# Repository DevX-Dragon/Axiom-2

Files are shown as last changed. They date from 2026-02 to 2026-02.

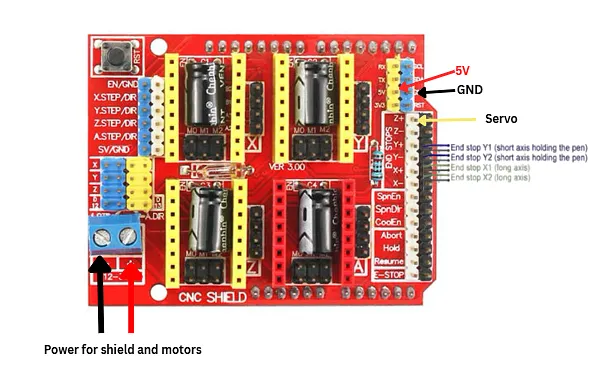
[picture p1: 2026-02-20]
images/CNC Wiring Diagram.png

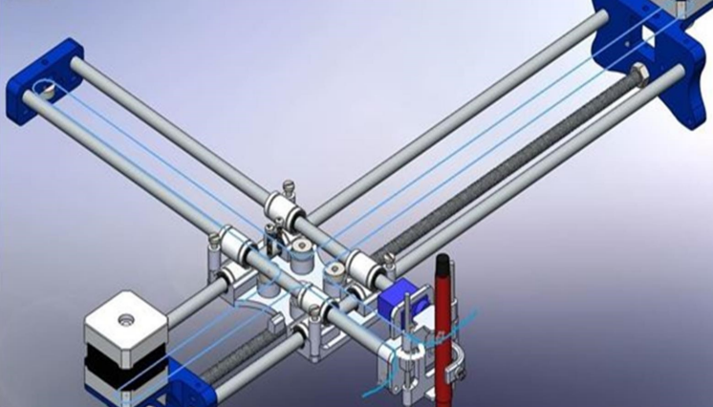
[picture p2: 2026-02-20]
images/BELT DIAGRAM.png

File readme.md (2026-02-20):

# Axiom-2 🤖🖊️
YO. Welcome to Axiom-2. It’s a CNC drawing machine that basically does my homework (not really, don't tell my teacher). I built this because I wanted a robot that draws better than me.

## What is this?
It’s a "Drawing Bot" that uses an Arduino Uno and a CNC Shield to move a pen around. It runs on GRBL (which is basically the brain) with some tiny tweaks I made so it doesn't freak out.

## Images
### Full Render
Full Render
(still in prodcution so not fully rendered)

### Belt Diagrams
Belt Diagram EXCIL DRAW 2
BELT DIAGRAM

### CNC Overview
CNC Wiring Diagram

## Cool Stuff Inside
**The Brain:** Arduino Uno + CNC Shield (v3)

**Firmware:** GRBL (hacked a bit)

**The Parts:** I put the BOM (Bill of Materials) in the .xlsx file above. It has all the nuts, bolts, and rods you need to buy.

**Pictures:** Check the /images folder to see what it actually looks like.

## How to use it (I think)
**Flash it:** Get the GRBL firmware onto the Arduino.

**Wire it:** Plug the stepper motors into the shield. Don't blow it up.

**Software:** Use something like Universal Gcode Sender (UGS) to send your drawings to the bot.

**Draw:** Put a pen in the holder and watch it go zoom.

## Hardware
I put the CAD files/designs in the /hardware folder. If you have a 3D printer, you can probably make this yourself.

## 🛠️ Axiom-2 Official BOM (with links!!)

| Product Name | Qty | Price (ea) | Total | Notes |
| :--- | :---: | :--- | :--- | :--- |
| [**Nema 17 Stepper Motor**](https://www.duino.lk/product/nema-17-stepper-motor-bipolar-1-8deg-1-5a-42ncm-42x42x40mm/) | 2 | $8.07 | $16.14 | Bipolar version |
| [**Linear Rod M8 (1m)**](https://www.duino.lk/product/1000mm-8mm-smooth-shaft/) | 2 | $5.81 | $11.62 | Need 2x 450mm and 2x 350mm |
| **Linear Rod 3mm** | 2 | - | $0.00 | Salvaging from a CDROM |
| **Threaded Rod M8 x 480mm** | 1 | - | $0.00 | Still haven't found a link for this |
| [**LM8UU Bearings**](https://www.duino.lk/product/lm8luu-lm20luu-ball-bearings/) | 8 | $1.45 | $11.60 | Standard sliders |
| [**SG90 Servo Motor**](https://www.duino.lk/product/servo-motor-sg90-9g-micro-servo-motor/) | 1 | $1.81 | $1.81 | Pen lift go brrrr |
| **Spring** | 1 | - | $0.00 | From a ballpoint pen lol |
| [**GT2 Pulley (16T)**](https://www.duino.lk/product/gt2-16t-16-teeth-5mm-bore/) | 2 | $0.97 | $1.94 | 5mm bore |
| [**Bearing 624zz**](https://www.duino.lk/product/624zz-ball-bearing/) | 5 | $0.48 | $2.40 | Tiny bearings |
| [**GT2 Belt (1m)**](https://www.duino.lk/product/gt2-6mm-width-2gt-pu-transmission-timing-belt/) | 2 | $1.61 | $3.22 | Buying 2m total |
| [**CNC Shield + Uno + Drivers**](https://www.duino.lk/product/cnc-shield-v3-0-uno-r3-4pcs-a4988-drivers/) | 1 | $20.97 | $20.97 | Cheaper as a kit |
| [**Jumper Connectors**](https://www.duino.lk/product/2-pin-jumper-connector-stud-2-54mm-standard/) | 1 | $0.32 | $0.32 | |
| [**12V 2A Power Supply**](https://www.duino.lk/product/power-supply-adapter-3-pin-ac-dc-12v-2a/) | 1 | $2.42 | $2.42 | |
| **3D Printing (Legion)** | 1 | $30.00 | $30.00 | |
| **Exchange Tax** | - | - | $5.00 | |
| **Shipping** | - | - | $5.00 | |
| **TOTAL** | | | **$112.44** | |
> (THIS IS USING A LOCAL ONLY ELECTRONICS STORE. IF YOU'RE GOING TO HAVE TO SOURCE IT YOURSELF. USE AMAZON , ALIEXPRESS , TEMU)
> THERE ARE STILL NUTS , WASHERS , ETC YOU NEED BUY SEPERATELY

Made by DevX-Dragon 🐉
(If it breaks, its not my fault lol)

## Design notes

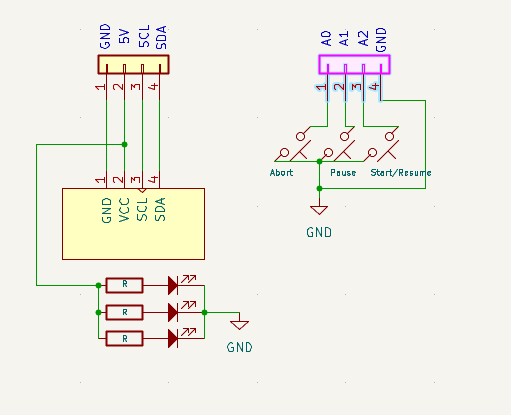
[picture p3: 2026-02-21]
images/Controller Board Schematics.png

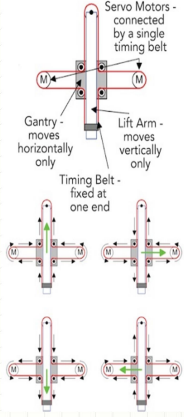
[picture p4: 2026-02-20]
images/Belt Diagram EXCIL DRAW 2.png

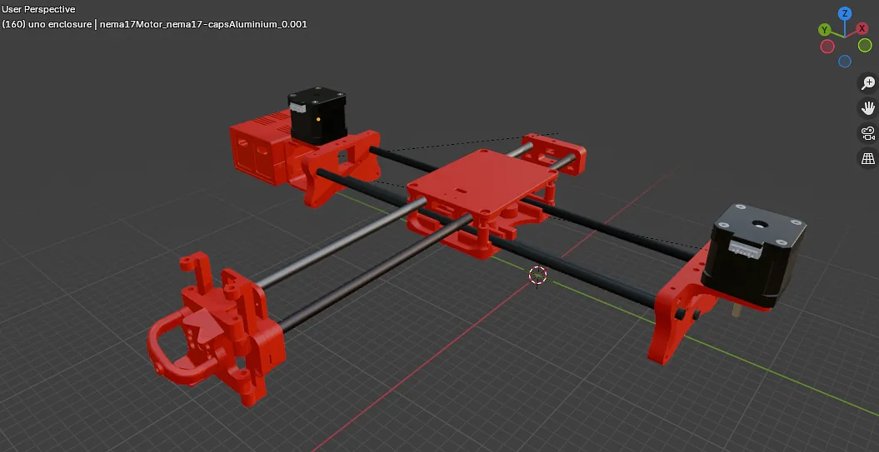
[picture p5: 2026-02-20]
images/Full Render.png

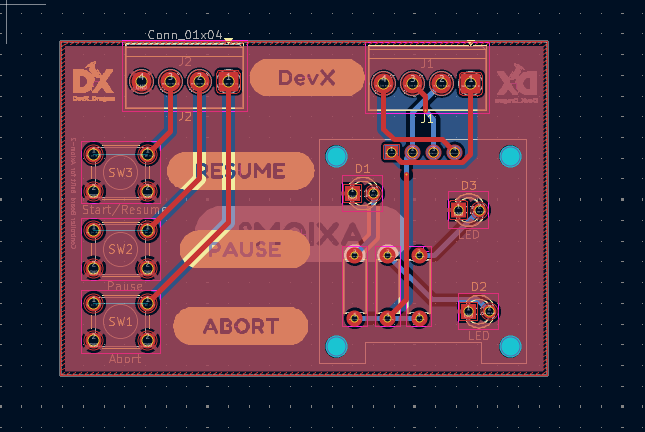
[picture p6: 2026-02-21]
images/Controller Board PCB.png

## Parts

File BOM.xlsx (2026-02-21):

Product Name | Quanity | Price Per Unit | Total Price | Link | Additional Notes
Nema 17 Stepper Motor Bipolar 1.8deg 1.5A 42Ncm 42x42x40mm 4 Wires with 1m | 2 | $8.07 | $16.14 | https://www.duino.lk/product/nema-17-stepper-motor-bipolar-1-8deg-1-5a-42ncm-42x42x40mm/ | bipolar version
Linear Rod M8 x 450mm + 350mm | 2 | $5.81 | $11.62 | https://www.duino.lk/product/1000mm-8mm-smooth-shaft/ | I need x2 450mm and x2 350mm for x and y axis. Buying 2 m totally
Linear Rod 3mm | 2 |  | $0.00 |  | Cant seem to find it anywhere, will have to get from a CDROM
Threaded Rod M8 x 480mm |  |  | $0.00 |  | Havent found it yet
LM8UU Bearings | 8 | $1.45 | $11.60 | https://www.duino.lk/product/lm8luu-lm20luu-ball-bearings/
SG90 Servo Motor | 1 | $1.81 | $1.81 | https://www.duino.lk/product/servo-motor-sg90-9g-micro-servo-motor/
Spring |  |  | $0.00 |  | From Ball point pen lol
GT2 Pulley, 16 teeth | 2 | $0.97 | $1.94 | https://www.duino.lk/product/gt2-16t-16-teeth-5mm-bore/
Bearing 624zz | 5 | $0.48 | $2.40 | https://www.duino.lk/product/624zz-ball-bearing/
GT2 6mm Width 2GT PU (Steel Transmission Timing Belt 1m | 2 | $1.61 | $3.22 | https://www.duino.lk/product/gt2-6mm-width-2gt-pu-transmission-timing-belt/ | Have to buy 2 of these for 2m
CNC Shield V3.0 + uno R3 + 4pcs a4988 drivers | 1 | $20.97 | $20.97 | https://www.duino.lk/product/cnc-shield-v3-0-uno-r3-4pcs-a4988-drivers/ | Buying the Kit is cheaper than buying them individually
Jumper Connector | 1 | $0.32 | $0.32 | https://www.duino.lk/product/2-pin-jumper-connector-stud-2-54mm-standard/
12V 2A Power Supply | 1 | $2.42 | $2.42 | https://www.duino.lk/product/power-supply-adapter-3-pin-ac-dc-12v-2a/
3D Printing (Printing Legion) | 1 | $30.00 | $30.00
OLED 0.96 inch 128X64 OLED Display | 1 | $0.50 | $0.50 | https://www.duino.lk/product/oled-128x64-display-module/
6x6x5mm Tactile Push Button Switch 2 pins Micro Switch | 3 | $0.07 | $0.20 | https://www.duino.lk/product/tactile-push-button-switch-2pins-6x6x5mm/
10PCS 220 Ohm 0.5W 5% Carbon Film Resistor | 1 | $0.13 | $0.13 | https://www.duino.lk/product/10pcs-220-ohm-0-5w-5-carbon-film-resistor/
White Diffused LED's 20 pcs | 1 | $0.32 | $0.32 | https://www.duino.lk/product/led-3mm-water-clear-20ma/
Exchange Tax |  |  | $5.00
Shipping |  |  | $5.00
Total |  |  | $113.58

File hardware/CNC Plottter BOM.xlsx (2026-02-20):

Product Name | Quanity | Link | Price Per Unit | Final Price
Nema 17 Stepper Motors | 2 | https://www.duino.lk/product/nema-17-stepper-motor-bipolar-1-8deg-1-5a-42ncm-42x42x40mm/ | $7.80 | $15.60
CNC Shield V3.0 + uno R3 + 4pcs a4988 drivers | 1 | https://www.duino.lk/product/cnc-shield-v3-0-uno-r3-4pcs-a4988-drivers/ | $20.94 | $20.94
12V 2A Orginal Power Supply Adapter 3 PIN AC/DC | 1 | https://www.duino.lk/product/12v-2a-orginal-power-supply-adapter/ | $2.90 | $2.90
Servo Motor SG90 9G Micro Servo Motor | 1 | https://www.duino.lk/product/servo-motor-sg90-9g/ | $1.13 | $1.13
1000mm 8mm Smooth Shaft Rod Diameter 8mm Length 1M *1Pcs | 2 | https://www.duino.lk/product/1000mm-8mm-smooth-shaft/ | $5.80 | $11.60
LM8LUU-LM20LUU Ball Bearings For CNC 3D Printers Parts Rail Linear *Long Rod Shaft Part | 8 | https://www.duino.lk/product/lm8luu-lm20luu-ball-bearings/ | $1.45 | $11.60
GT2 6mm Width 2GT PU Steel Transmission Timing Belt *1M | 2 | https://www.duino.lk/product/gt2-6mm-width-2gt-pu-transmission-timing-belt/ | $1.61 | $3.22
GT2 16T 16 Teeth 5mm Bore T16B5W10 10mm Width Timing Pulley | 2 | https://www.duino.lk/product/gt2-16t-16-teeth-5mm-bore/ | $0.97 | $1.94
M3 Iron Phillips Head Screws+Nuts Fastener 16mm | 15 | https://www.duino.lk/product/m3-iron-phillips-head-screws-nuts-fastener-3mm-30mm/ | $0.03 | $0.45
M3 Iron Phillips Head Screws+Nuts Fastener 6mm | 5 | https://www.duino.lk/product/m3-iron-phillips-head-screws-nuts-fastener-3mm-30mm/ | $0.02 | $0.10
M3 Bolt & Nut 3x20mm (Approx. 10pcs) (NB0007) | 1 | https://tronic.lk/product/m3-bolt-nut-3x20mm-approx-10pcs | $0.13 | $0.13
M3 Stainless Steel Plain Flat Washer (TA1606) | 10 | https://tronic.lk/product/m3-stainless-steel-plain-flat-washer | $0.02 | $0.19
Jumper Connectors (20pcs) | 1 | https://www.duino.lk/product/2-pin-jumper-connector-stud-2-54mm-standard/ | $0.40 | $0.40
624ZZ 4x13x5mm Steel Sealed Ball Bearing | 5 | https://www.duino.lk/product/624zz-ball-bearing/ | $0.48 | $2.40
3D Printed Parts (@souptik samanta on printing legion) |  |  | PENDING | PENDING
 |  |  |  | $72.60

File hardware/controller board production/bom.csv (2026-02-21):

Designator | Footprint | Quantity | Value | LCSC Part #
D1, D2, D3 | LED_D3.0mm | 3 | LED
J1, J2 | TerminalBlock_Phoenix_PT-1,5-4-3.5-H_1x04_P3.50mm_Horizontal | 2 | Conn_01x04
J4 | OLED_128x64 | 1 | OLED_128x64
R1, R2, R3 | R_Axial_DIN0207_L6.3mm_D2.5mm_P7.62mm_Horizontal | 3 | R
SW1 | SW_PUSH_6mm | 1 | Abort
SW2 | SW_PUSH_6mm | 1 | Pause
SW3 | SW_PUSH_6mm | 1 | Start/Resume

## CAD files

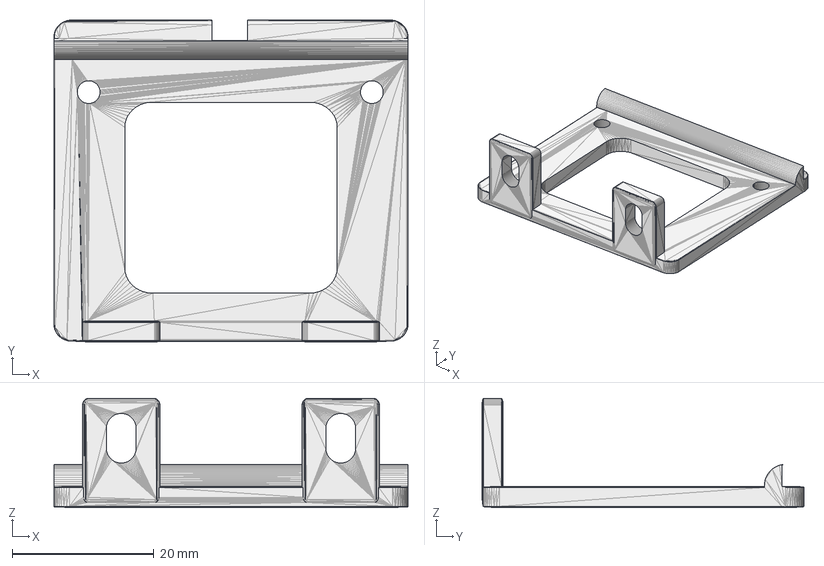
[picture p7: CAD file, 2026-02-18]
hardware/Step Files/UNO CASE MOUNT .step
50.0 x 45.5 x 15.4 mm

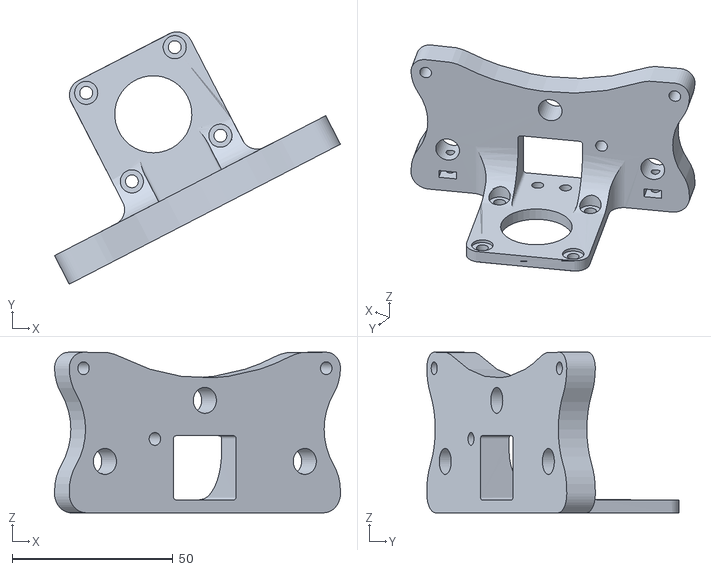
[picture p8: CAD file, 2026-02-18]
hardware/STL Files/X Support Right.stl
89.0 x 78.6 x 50.0

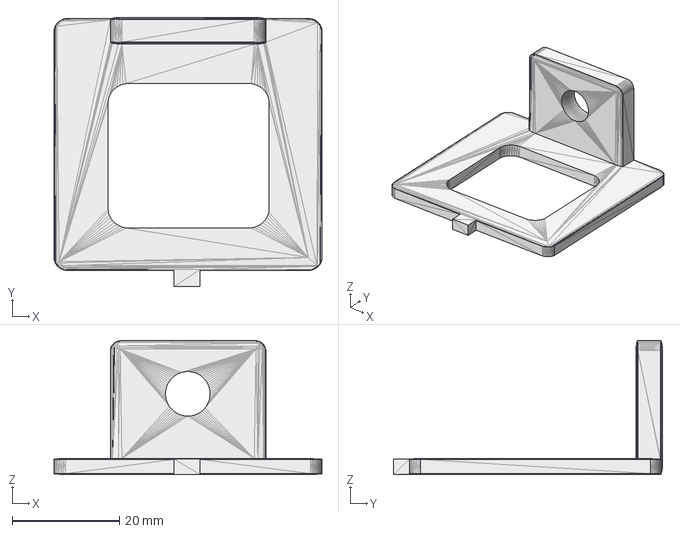
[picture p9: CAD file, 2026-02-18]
hardware/Step Files/uno case base mount.step
50.0 x 50.2 x 25.0 mm

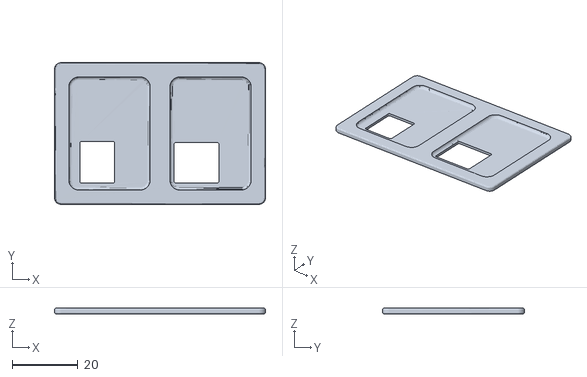
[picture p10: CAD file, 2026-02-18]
hardware/STL Files/CNC_Front.stl
64.0 x 43.0 x 1.80

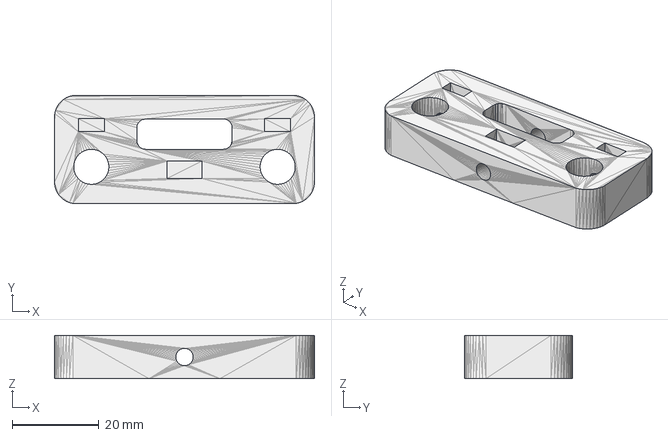
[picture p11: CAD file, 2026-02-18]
hardware/Step Files/Y Support Back.step
60.0 x 25.0 x 10.0 mm

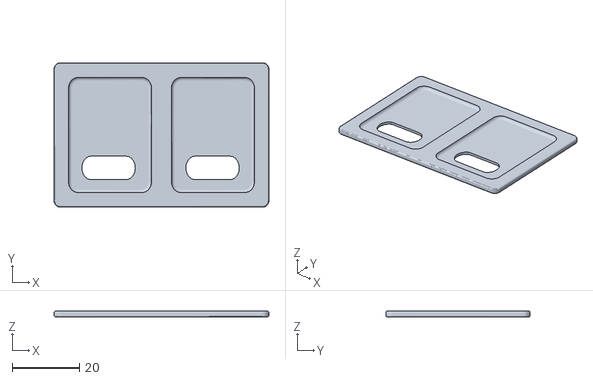
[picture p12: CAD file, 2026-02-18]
hardware/STL Files/CNC_Back.stl
64.0 x 43.0 x 1.80

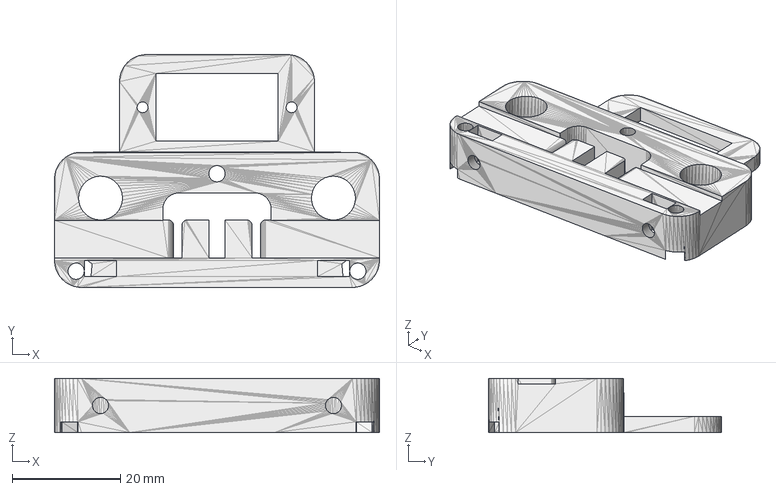
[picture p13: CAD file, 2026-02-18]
hardware/Step Files/Y Support Front.step
60.0 x 43.0 x 10.0 mm

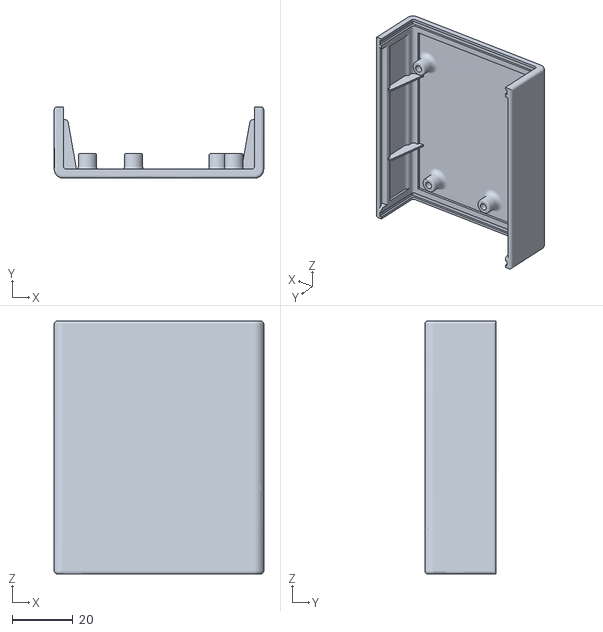
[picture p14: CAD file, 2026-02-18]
hardware/STL Files/CNC_Bottom.stl
69.0 x 23.5 x 83.3

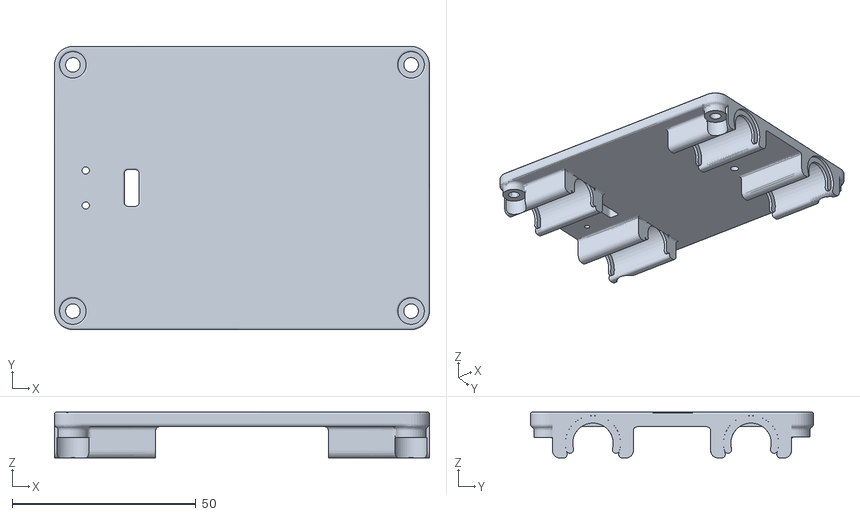
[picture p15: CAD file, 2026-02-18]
hardware/STL Files/TOP xy CLAMPSHELL.stl
102.0 x 77.0 x 12.5

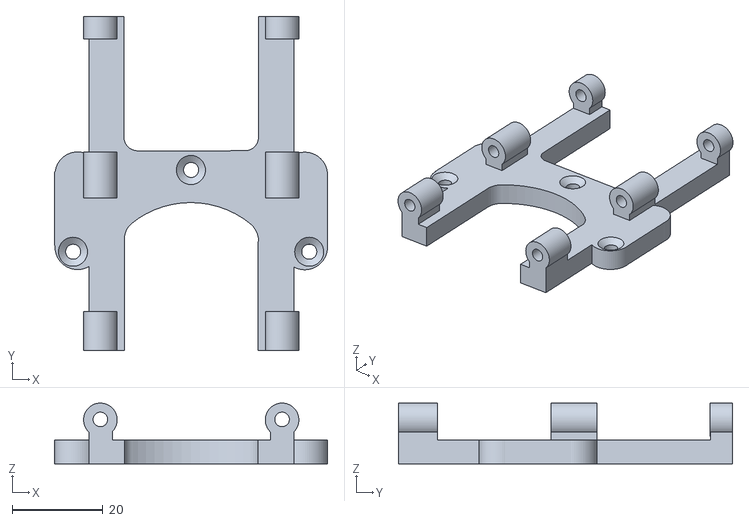
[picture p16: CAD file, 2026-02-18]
hardware/STL Files/Base Slider HEAVY DUTY.stl
60.1 x 73.6 x 13.4

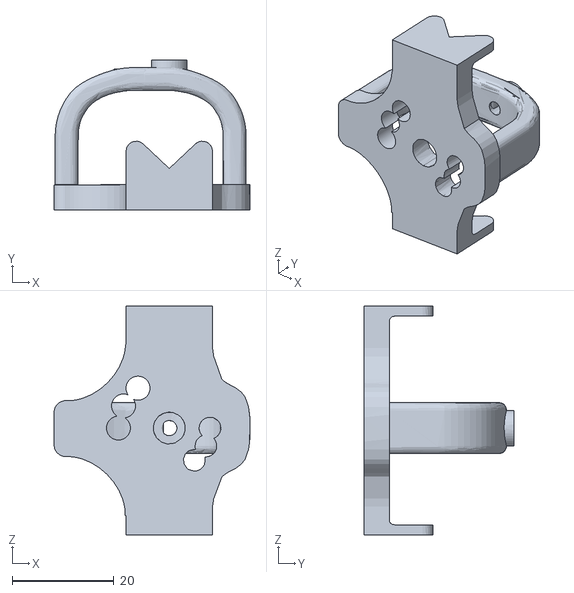
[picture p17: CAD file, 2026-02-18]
hardware/STL Files/Pen Holder .stl
38.5 x 29.5 x 45.0

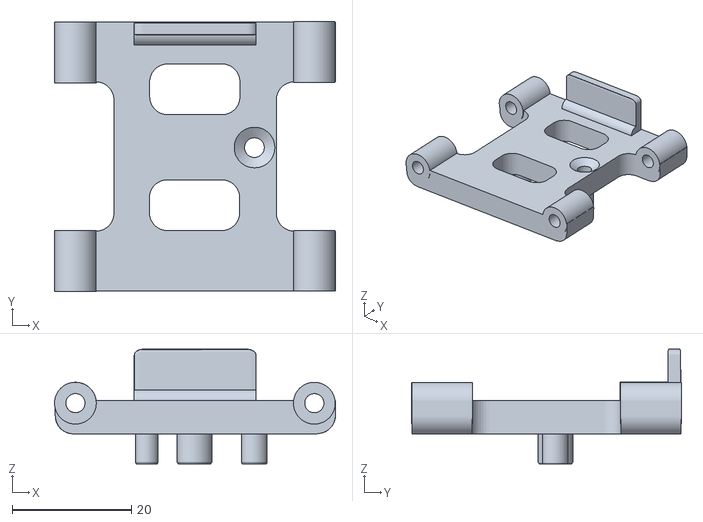
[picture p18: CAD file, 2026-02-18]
hardware/STL Files/Plain Slider .stl
47.0 x 45.2 x 19.2

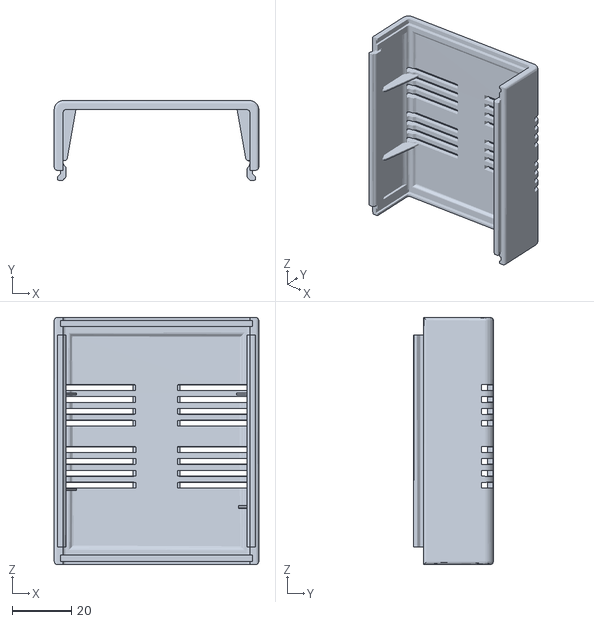
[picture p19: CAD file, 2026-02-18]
hardware/STL Files/CNC_TOP.stl
69.0 x 26.9 x 83.3

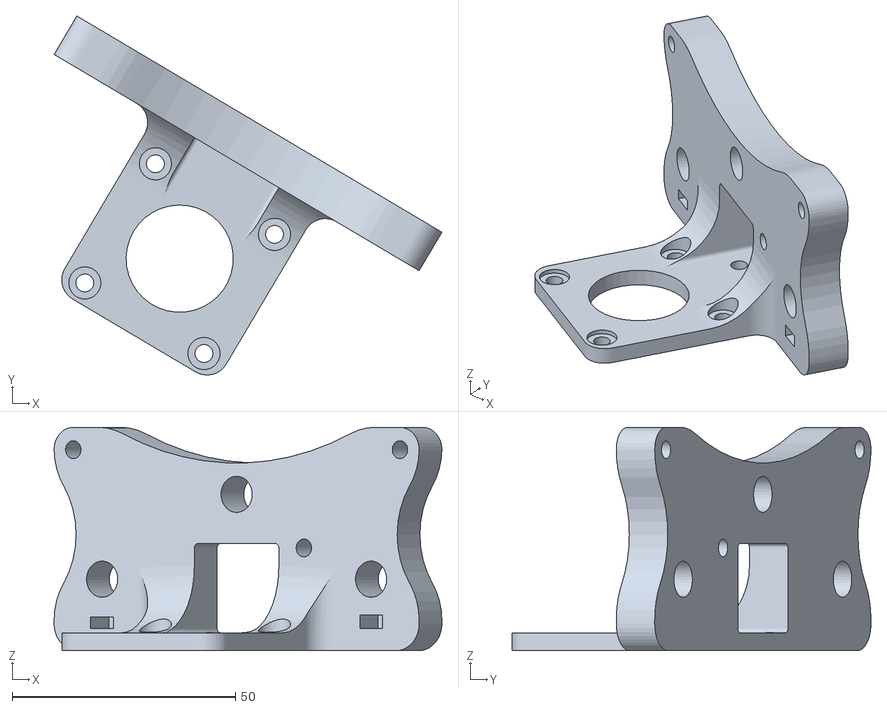
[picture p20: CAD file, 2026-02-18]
hardware/STL Files/X Support Left.stl
86.8 x 80.4 x 50.0

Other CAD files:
hardware/STL Files/Bottom xy CLAMPSHELL.stl
hardware/STL Files/UNO CASE MOUNT .stl
hardware/STL Files/Y Support Back.stl
hardware/STL Files/Y Support Front.stl
hardware/STL Files/uno case base mount.stl
hardware/Source Files [.blend]/Base Slider and Slider source (2).blend
hardware/Source Files [.blend]/Enclosure Mount Source.blend
hardware/Source Files [.blend]/Enclosure Mount.blend
hardware/Source Files [.blend]/Encloure FULL Source.blend
hardware/Source Files [.blend]/Pen Holder Source v1 .blend
hardware/Source Files [.blend]/Pen Holder Source.blend
hardware/Source Files [.blend]/TOP AND BOTTOM.blend
hardware/Source Files [.blend]/X Support (R&L) Source.blend
hardware/Source Files [.blend]/Y Support (F&B) Source.blend

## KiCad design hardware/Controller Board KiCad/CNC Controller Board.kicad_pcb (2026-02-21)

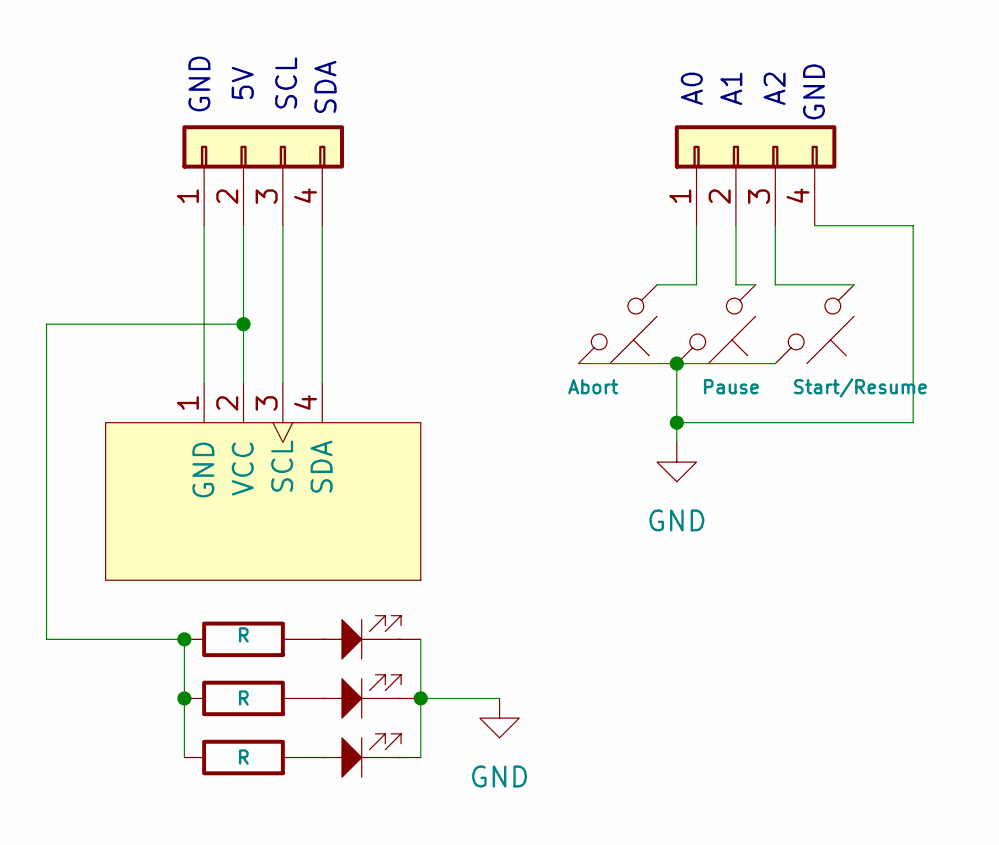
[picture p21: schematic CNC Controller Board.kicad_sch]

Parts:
D1, D2, D3: LED; LED_D3.0mm
J1, J2: Conn_01x04; TerminalBlock_Phoenix_PT-1,5-4-3.5-H_1x04_P3.50mm_Horizontal
J4: OLED_128x64
R1, R2, R3: R; R_Axial_DIN0207_L6.3mm_D2.5mm_P7.62mm_Horizontal
SW1: Abort; SW_PUSH_6mm
SW2: Pause; SW_PUSH_6mm
SW3: Start/Resume; SW_PUSH_6mm

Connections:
GND: D1.1, D2.1, D3.1, J2.4, SW1.2, SW2.2, SW3.2
unnamed: D1.2, R1.2
unnamed: D2.2, R2.2
unnamed: D3.2, R3.2
unnamed: J1.1, J4.1 (GND)
unnamed: J1.2, J4.2 (VCC), R1.1, R2.1, R3.1
unnamed: J1.3, J4.3 (SCL)
unnamed: J1.4, J4.4 (SDA)
unnamed: J2.1, SW1.1
unnamed: J2.2, SW2.1
unnamed: J2.3, SW3.1

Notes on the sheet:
SCL
GND
SDA

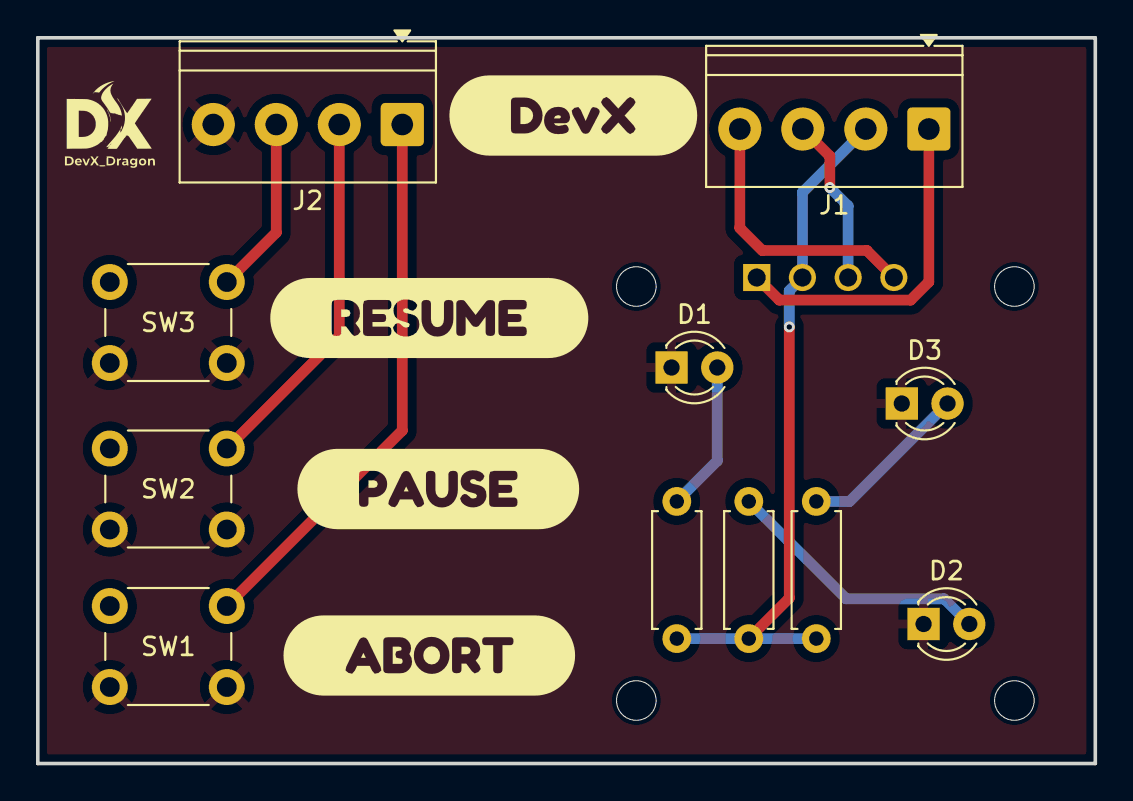
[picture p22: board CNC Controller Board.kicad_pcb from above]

Board: 2 copper layers, 58.8 x 40.3 mm, 17 parts (1 on the bottom side), 11 nets.

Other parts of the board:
kibuzzard-69997A6C: G***; kibuzzard-69997A6C
kibuzzard-699976DE: G***; kibuzzard-699976DE
kibuzzard-699976F2: G***; kibuzzard-699976F2
kibuzzard-699976FE: G***; kibuzzard-699976FE
kibuzzard-699979CF: G***; kibuzzard-699979CF

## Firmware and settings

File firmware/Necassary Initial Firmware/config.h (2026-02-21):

// --- GRBL CONFIGURATION FOR Axiom-2 ---

#define COREXY 
#define VARIABLE_SPINDLE // so the z-axis is tied to D11 now.
#define SPINDLE_PWM_MIN_VALUE 5     // Pen Down position (the range btw)
#define SPINDLE_PWM_MAX_VALUE 20    // Pen Up position (the range btw)
#define INVERT_LIMIT_PIN_MASK ((1<<X_LIMIT_BIT)|(1<<Y_LIMIT_BIT)|(1<<Z_LIMIT_BIT)) //for the sheild
#define BAUD_RATE 115200 // using so i can debug fast if i need to

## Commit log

2026-02-18 Axiom-2: Initial Build
    [Base Slider HEAVY DUTY.stl, Base Slider and Slider source (2).blend, Bottom xy CLAMPSHELL.stl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]
2026-02-20 Initial BOM push v1
    [CNC Plottter BOM.xlsx]
2026-02-20 BOM Upload
    [CNC Plottter BOM.xlsx]
2026-02-20 BOMv1 TO ROOT DIR
    [CNC Plottter BOM.xlsx]
2026-02-20 initial image upload
    [CNC Plottter BOM.xlsx, Current BOM .xlsx]
2026-02-20 Added some firmware tweals , servo motor needs a special firmware edit as well
    [Current BOM .xlsx]
2026-02-21 Firmware Upload v1
    [cpu_map.h, defaults.h]
2026-02-21 Adding Controller PCB Files
    [CNC Controller Board.kicad_pcb, CNC Controller Board.kicad_sch, bom.csv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]
2026-02-21 BOM Modifcations for PCB
    [BOM.xlsx, Current BOM .xlsx]
